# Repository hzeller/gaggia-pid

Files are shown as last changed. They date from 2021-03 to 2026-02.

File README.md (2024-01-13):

PID controller for Gaggia Classic
=================================

# Temperature Sensor
Using the [Max31725] for nice high accuracy and fast temperature updates. Also
a bit overengineered, but that is what I had lying around.

The sensor is on a little PCB (which you find in the
[sensor-mount/](./sensor-mount) directory. Glued into the existing brass
screw-cups the original bimetallic sensor was in (using JB Weld, which is
a sufficiently high-temperature epoxy), then wired up with silicone wiring and
sealed with silicone.

Mount on the side of the boiler where the original brew temp sensor was.

PCB            | Preparing mount | Glued in cup | Sealed
---------------|-----------------|--------------|--------
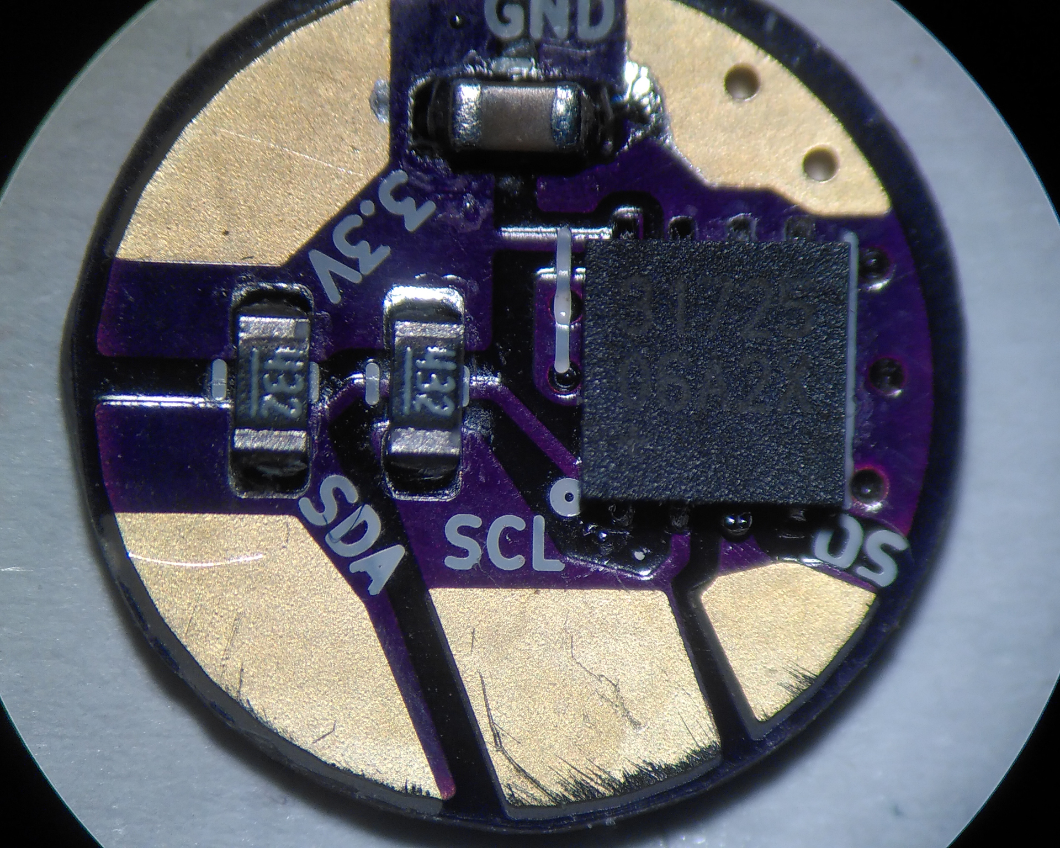
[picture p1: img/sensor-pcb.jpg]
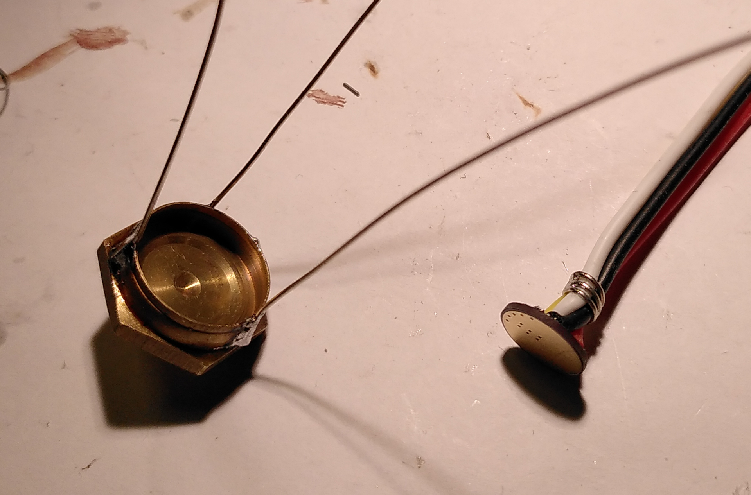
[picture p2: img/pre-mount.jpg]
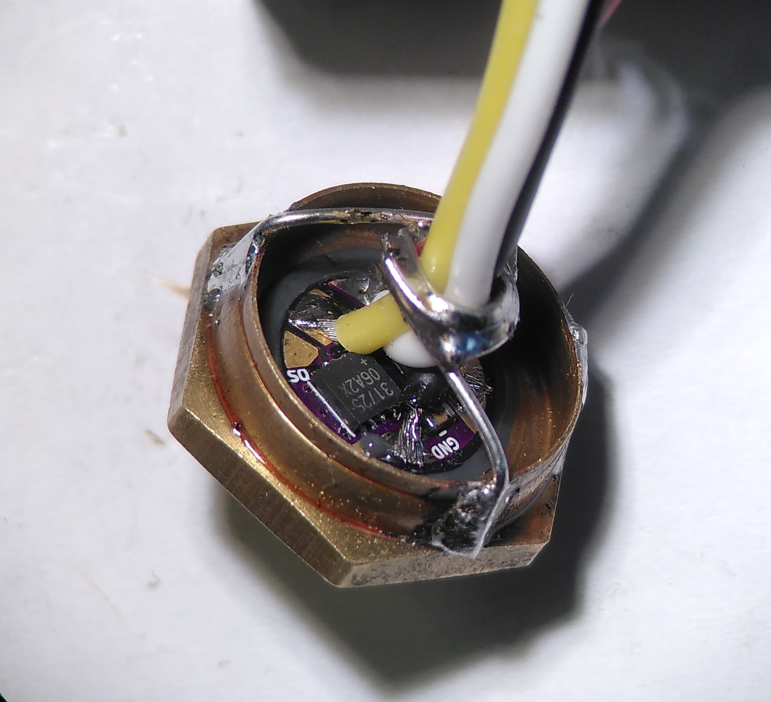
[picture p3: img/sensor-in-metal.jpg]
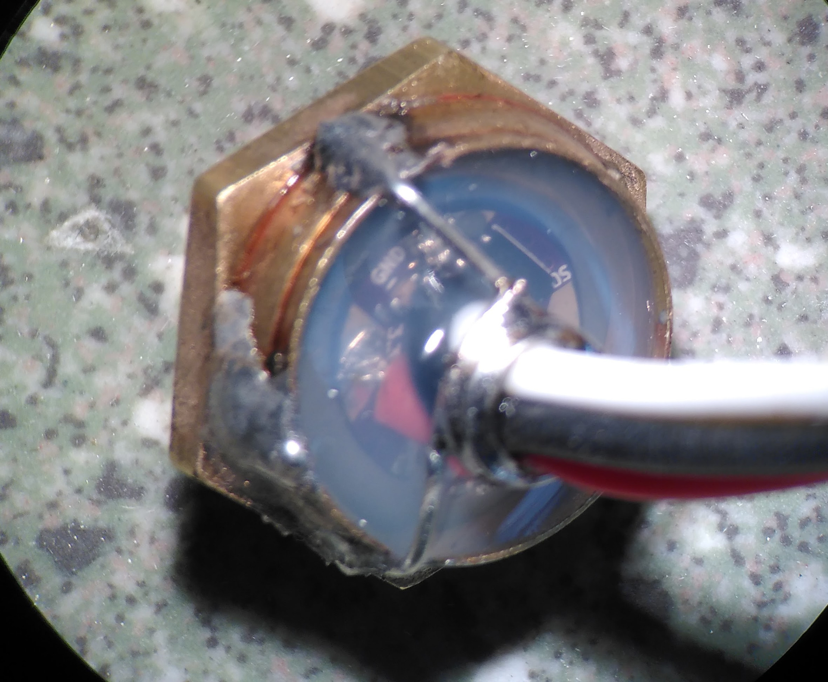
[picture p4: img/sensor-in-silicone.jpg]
 |  |  | 

# PID Controller

Runs on a conventional Arduino Nano.

To program, get avr-gcc and avrdude. The Makefile takes care of compiling
and flashing:

```
cd firmware
make flash
```

The sytem is powered with a sealed 5V power supply CUI PSK-3D-5.
The Solid State Relay is a Panasonic AQJ112V.

The USB connector is arranged in a way that it is reachable through one of the
opening on the back. From the front, the machine is entirely unaltered (unlike
many of the somewhat ugly PID mods of this machine).

You connect with a serial console to the PID controller, adjust
PID parameters and watch an ASCII-art 'graphical' output of the temperature
sensor (see the picture with the Laptop in view and the rising temperature
displayed).

PID parameters can be tuned with the interface presented on the serial
interface and stored in EEPROM.

Serial interface running by default on 38400 bps:

```bash
tio -b 38400 /dev/ttyUSB0
```

Menu:
```
#            ☕ Gaggia PID controller
#(c) 2021 Henner Zeller  |  GNU Public License
#Commands
#       l - Start log to console. Stop with any key.
#       L - Ditto. With 'graph'
#       n - Now. Print PID parameters, last temp and control out.
#
#       s <setpoint> - set setpoint.
#       p <Kp>       - set proportional gain.
#       i <Ki>       - set integral gain.
#       d <Kd>       - set derivative gain.
#
#       w - Write PID parameters to EEPROM.
#       r - Restore PID parameters from EEPROM.
#       h - This help
```

Components         | Mounted | Back  | Settings via USB
-------------------|---------|-------|--------------------------
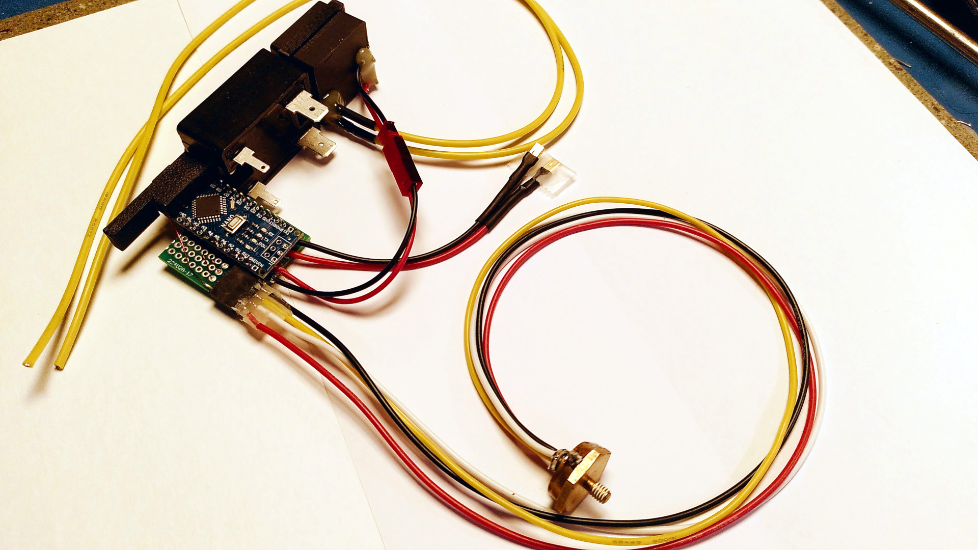
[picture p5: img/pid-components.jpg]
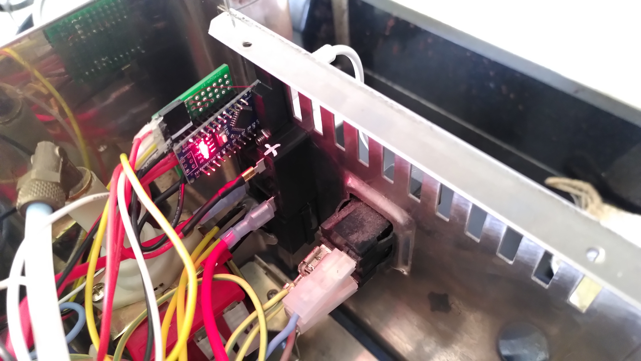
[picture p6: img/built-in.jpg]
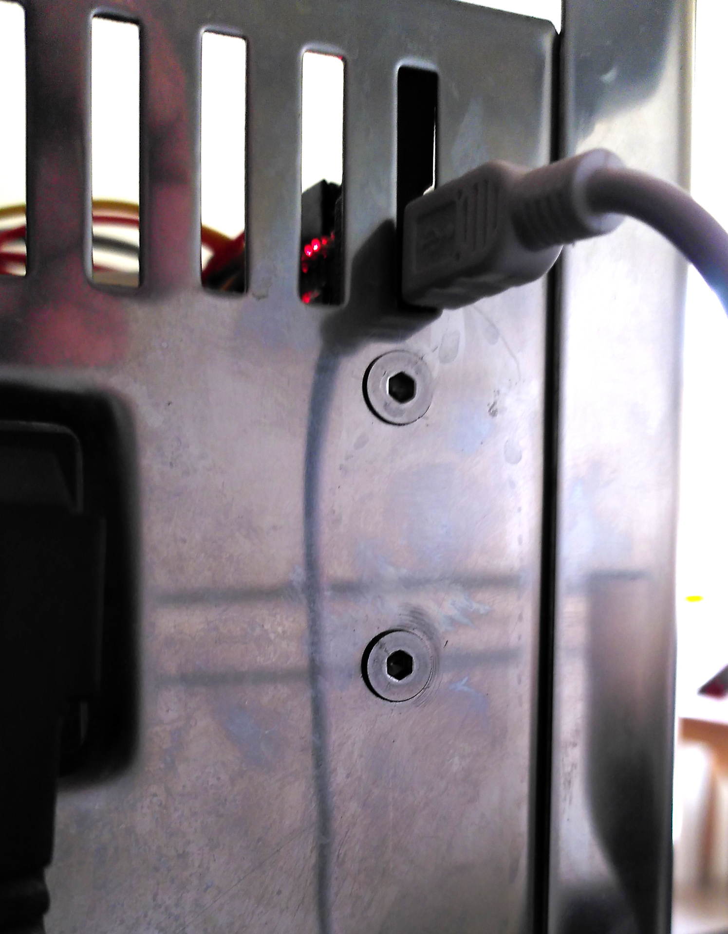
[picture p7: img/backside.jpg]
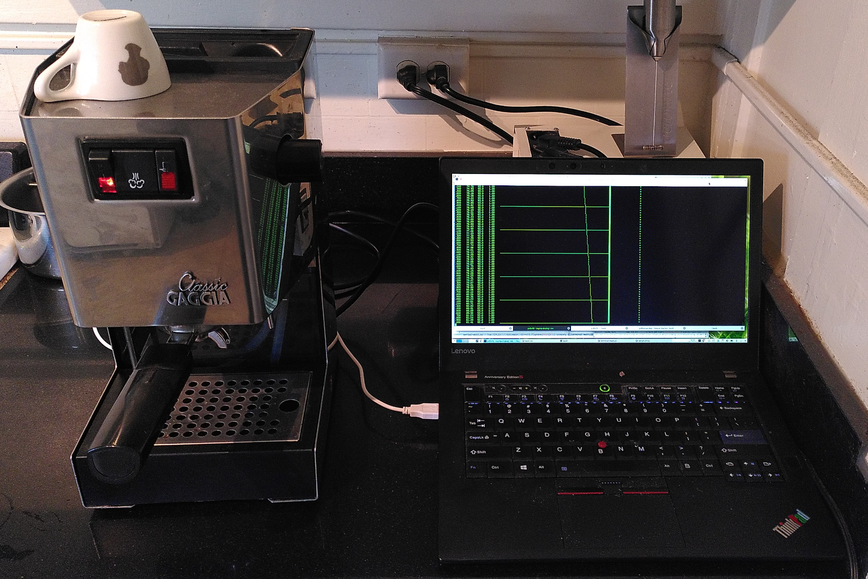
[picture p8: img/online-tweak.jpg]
 |  |  | 

[Max31725]: https://datasheets.maximintegrated.com/en/ds/MAX31725-MAX31726.pdf

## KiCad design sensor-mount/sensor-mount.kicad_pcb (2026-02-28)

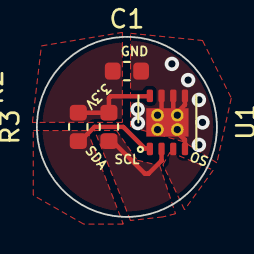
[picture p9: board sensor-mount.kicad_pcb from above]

Board: 2 copper layers, 10.0 x 10.0 mm, 4 parts (0 on the bottom side), 4 nets.

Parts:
C1: 220n; C_0603_1608Metric
R2, R3: 4k7; R_0603_1608Metric
U1: MAX31725; DFN-8-1EP_3x3mm_P0.65mm_EP1.7x2.05mm

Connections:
/SCL: R2.2, U1.2 (SCL)
/SDA: R3.2, U1.1 (SDA)
GND: C1.2, U1.4 (GND), U1.5 (A2), U1.6 (A1), U1.7 (A0), U1.9 (EP)
VCC: C1.1, R2.1, R3.1, U1.8 (VDD)

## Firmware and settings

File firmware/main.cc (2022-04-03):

// -*- mode: c++; c-basic-offset: 2; indent-tabs-mode: nil; -*-
//
// Copyright (C) 2021 Henner Zeller <h.zeller@acm.org>
//
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
#include <math.h>
#include <stdlib.h>
#include <string.h>

#include <avr/eeprom.h>
#include <avr/interrupt.h>
#include <avr/io.h>
#include <avr/sleep.h>

#include "i2c-master.h"
#include "max31725.h"
#include "pid.h"
#include "progmem.h"
#include "serial-com.h"
#include "serial-util.h"
#include "strfmt.h"

/* Note, we have plenty of flash, so we use the luxory of float numbers */

/*
 * Regular interval to take measurements and calculate a new PID control output
 */
static constexpr uint16_t kTimeBaseMs = 50;

static struct ConfigData {
  char dummy;  // Leave first char free, sometimes containing garbage.

  // PID info.
  float setpoint;
  float kp;
  float ki;
  float kd;

  void Write() {
    eeprom_write_float(&setpoint, setpoint);
    eeprom_write_float(&kp, kp);
    eeprom_write_float(&ki, ki);
    eeprom_write_float(&kd, kd);
  }
  void Read() {
    setpoint = eeprom_read_float(&setpoint);
    kp = eeprom_read_float(&kp);
    ki = eeprom_read_float(&ki);
    kd = eeprom_read_float(&kd);
  }
} EEMEM eeConfigData;

// Read number from serial and indicate if it was successful.
// Pre-fill the editline with the existing number with given digits.
static bool readNumber(SerialCom *comm, float *value, int digits) {
  char buffer[10];
  strcpy(buffer, strfmt_float(*value, digits));
  const char *str = readln(comm, buffer, sizeof(buffer), true);
  char *endptr = nullptr;
  float converted = strtod(str, &endptr);
  if (endptr != str) {
    *value = converted;
    println(comm, _P(" ✓"));
    return true;
  } else {
    println(comm, _P(" ✗ (not changed)"));
    return false;
  }
}

// A slow PWM of the heater. There is not much point in high-speed PWM with
// a zero-cross SSD, so we manually trigger with a timer interrupt.
// We go through one full cycle in kRange time interrupts.
//
// For safety, the value needs to be set for each cycle individually, otherwise
// we fail-safe to zero output.
class HeaterPWM {
  static constexpr uint8_t PORTB_LED_BIT = (1<<5);
  static constexpr uint8_t PORTD_SSR_BIT = (1<<3);

public:
  static constexpr uint8_t kRange = 32;

  HeaterPWM() {
    DDRB |= PORTB_LED_BIT;
    DDRD |= PORTD_SSR_BIT;
    SetOn(false);  // Safe starting point.
  }

  // Value of 0..1.0
  // For safety, needs to be actively set once per period, otherwise will
  // fall-back to zero. This prevents lock-up situations.
  void SetValue(float v) {
    if (v < 0.0) v = 0;
    if (v > 1.0) v = 1.0;
    value_ = v * kRange;
  }

  void HandleTimeInterrupt(uint8_t global_time) volatile {
    if ((global_time % kRange) == 0) {
      pwm_state_ = value_;
      value_ = 0;  // Will require to SetValue() again.
    }

    SetOn(pwm_state_ != 0);
    if (pwm_state_ > 0) --pwm_state_;
  }

private:
  void SetOn(bool b) volatile {
    if (b) {
      PORTB |= PORTB_LED_BIT;
      PORTD |= PORTD_SSR_BIT;
    } else {
      PORTB &= ~PORTB_LED_BIT;
      PORTD &= ~PORTD_SSR_BIT;
    }
  }

  volatile uint8_t value_ = 0;      // Range from 0x00..kRange
  volatile uint8_t pwm_state_ = 0;  // Current PWM counter.
};

// There is only one global instance, accessible to the timer interrupt
static HeaterPWM sHeater;

/*
 * Setting up timer to trigger an interrupt every kTimeBaseMs
 */
static constexpr uint16_t kTimerCounts = F_CPU / 256 * kTimeBaseMs / 1000;
static constexpr uint16_t kTimerRegister = 65535 - kTimerCounts;

// Global time, increasing with timer interrupt. Wrapping around at 8 bit.
volatile uint8_t sGlobalTime = 0;

ISR(TIMER1_OVF_vect) {
  sGlobalTime++;
  TCNT1 = kTimerRegister;
  sHeater.HandleTimeInterrupt(sGlobalTime);
}

void initTimer() {
  TCNT1 = kTimerRegister;
  TCCR1A = 0x00;
  TCCR1B = (1 << CS12); // prescale 256 (also see kTimerCounts)
  TIMSK1 = (1 << TOIE1);
}

// Print temperature and control value, and show in 'graphical' form.
void printTemp(SerialCom *com, bool markline,
               float measured, float control_value,
               float target_temp,
               bool with_graph) {
  const ProgmemPtr vt100Underline = _P("\e[4m");
  const ProgmemPtr vt100Inverse   = _P("\e[7m");
  const ProgmemPtr vt100Reset     = _P("\e[0m");

  // Raw values, formatted with tab to be easily parsed if needed.
  printRAM(com, strfmt_float(measured, 2));
  com->write('\t');
  printRAM(com, strfmt_float(target_temp, 1));
  com->write('\t');
  printRAM(com, strfmt_float(control_value, 2));
  com->write('\t');

  if (!with_graph) {
    println(com);
    return;
  }

  control_value *= 100.0f;  // Display in percent.

  // Useful for human consumption: some graph representation of above values
  constexpr float kBaselineOffset = 15;  // Cut off boring lower part.
  const uint8_t degree_display = measured - kBaselineOffset;
  const uint8_t target_display = target_temp > kBaselineOffset ?
    target_temp - kBaselineOffset : 0;
  uint8_t max_run = target_display;
  if (degree_display > max_run) max_run = degree_display;
  if (control_value > max_run)  max_run = control_value;

  const int decidegrees = 10.0f * measured;
  bool reset_needed = markline || target_display > 0;
  if (markline) print(com, vt100Underline);
  for (uint8_t s = 0; s < max_run+1; ++s) {
    // The target temperature is an inverted character cell, so that we can
    // see the temperature line 'underneath'.
    if (s > 0 && s == target_display) print(com, vt100Inverse);

    if (s == degree_display) {     // These are full degrees
      switch (decidegrees % 10) {  // Graphically divide decis into sub-blocks
      case 0: case 1: case 2:         print(com, _P("\u258f")); break;
      case 3: case 4: case 5: case 6: print(com, _P("|"));      break;
      case 7: case 8: case 9:         print(com, _P("\u2595")); break;
      }
    }
    else if (s == (uint8_t)control_value)
      com->write('*');
    else
      com->write(' ');

    if (s > 0 && s == target_display) {
      print(com, vt100Reset);
      reset_needed = false;
    }
  }

  if (reset_needed) print(com, vt100Reset);
  println(com);
}

void printUsage(SerialCom *com) {
  // Prefix all lines with '#' to make it easy to filter out lines meant
  // for human consumption.
  print(com,
        _P("#\e[7m            ☕ Gaggia PID controller            \e[0m\r\n"
           "#(c) 2021 Henner Zeller  |  GNU Public License\r\n"
           "#Commands\r\n"
           "#\tl - Start log to console. Stop with any key.\r\n"
           "#\tL - Ditto. With 'graph'\r\n"
           "#\tn - Now. Print PID parameters, last temp and control out.\r\n"
           "#\r\n"
           "#\ts <setpoint> - set setpoint.\r\n"
           "#\tp <Kp>       - set proportional gain.\r\n"
           "#\ti <Ki>       - set integral gain.\r\n"
           "#\td <Kd>       - set derivative gain.\r\n"
           "#\r\n"
           "#\tw - Write PID parameters to EEPROM.\r\n"
           "#\tr - Restore PID parameters from EEPROM.\r\n"
           "#\th - This help\r\n"
           ));
}

int main() {
  I2CMaster::Init();
  initTimer();

  // PID interval once per full PWM cycle.
  PID pid(HeaterPWM::kRange * kTimeBaseMs * 0.001);
  Max31725TempSensor sensor;
  SerialCom com;

  uint8_t last_measure_period = 0;

  float measured_temp = 42.0;
  float pid_control_output = 0.0f;

  // Logging enable status and its current time.
  bool logging = false;
  bool logging_with_graph = false;
  uint16_t log_time = 0;

  // Serial line connect apparently resets Arduino Nano.
  // Use that as an opportunity to print welcome and usage message.
  printUsage(&com);

  eeConfigData.Read();
  pid.FromConfig(eeConfigData);

  // Get ready to sleep. We're only doing anything when timer or serial calls.
  sleep_enable();
  sei();

  const ProgmemPtr kLoggingCSVHeader = _P("TIME\tTEMP\tTARGET\tCONTROL");
  for (;;) {
    sleep_cpu();  // Wake on interrupts from timer or serial.

    if (sGlobalTime != last_measure_period) {  // timer triggered
      last_measure_period = sGlobalTime;
      measured_temp = sensor.GetTemp();

      // Update the PID just before the heater starts its next PWM cycle.
      if (last_measure_period % HeaterPWM::kRange == HeaterPWM::kRange - 1) {
        pid_control_output = pid.Update(measured_temp);
        sHeater.SetValue(pid_control_output);
      }

      if (logging) {
        printRAM(&com, strfmt(log_time, 3));
        com.write('\t');
        printTemp(&com, log_time==0, measured_temp, pid_control_output,
                  pid.setpoint, logging_with_graph);
        log_time += kTimeBaseMs;
        log_time %= 1000;
      }
    }

    // Check for commands.
    while (com.read_available()) {
      const char c = com.read();
      if (logging) {   // stops at any key. Consume it.
        logging = false;
        println(&com, _P("# logging stopped."));
        continue;
      }
      switch (c) {
      case 'l':    // Trigger logging.
      case 'L':    // ... with graph.
        logging = true;
        logging_with_graph = (c == 'L');
        println(&com, _P("# logging started. Stop with any key."));
        println(&com, kLoggingCSVHeader);
        break;

      case 's':
        print(&com, _P("set setpoint = "));
        readNumber(&com, &pid.setpoint, 1);
        pid.Sanitize();
        pid.Print(&com, false);
        break;

      case 'p':
        print(&com, _P("set Kp = "));
        readNumber(&com, &pid.kp, 3);
        pid.Sanitize();
        pid.Print(&com, false);
        break;

      case 'i':
        print(&com, _P("set Ki = "));
        readNumber(&com, &pid.ki, 3);
        pid.Sanitize();
        pid.Print(&com, false);
        break;

      case 'd':
        print(&com, _P("set Kd = "));
        readNumber(&com, &pid.kd, 3);
        pid.Sanitize();
        pid.Print(&com, false);
        break;

      case 'n':
        pid.Print(&com, true);
        break;

      case 'w':
        println(&com, _P("Storing PID parameters to EEPROM."));
        pid.Print(&com, false);
        pid.ToConfig(&eeConfigData);
        eeConfigData.Write();
        break;

      case 'r':
        println(&com, _P("Restore PID parameters from EEPROM."));
        eeConfigData.Read();
        pid.FromConfig(eeConfigData);
        pid.Print(&com, false);
        break;

      case '\r': case '\n':
        // Ignore. Allows to idempotently reset logging before starting with 'l'
        break;

      default:
        com.write(c);
        println(&com, _P(" : Unknown command."));
        /* fallthrough */
      case '?': case 'h':
        printUsage(&com);
        break;
      }
    }
  }
}

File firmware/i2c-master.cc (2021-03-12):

// -*- mode: c++; c-basic-offset: 2; indent-tabs-mode: nil; -*-
//
// Copyright (C) 2018 Henner Zeller <h.zeller@acm.org>
//
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
#include "i2c-master.h"

#include <util/twi.h>
#include <avr/io.h>

// These are for ATMega328p
#define I2C_DDR       DDRC
#define I2C_PORT      PORTC
#define I2C_PORT_SDA  4
#define I2C_PORT_SCL  5

static constexpr uint32_t TX_SPEED = 400000;
static constexpr uint8_t PRESCALER = 1;
static constexpr uint8_t TWBR_val = (((F_CPU/TX_SPEED) / PRESCALER) - 16 ) / 2;

void I2CMaster::Init() {
  TWBR = TWBR_val;
}

void I2CMaster::Enable(bool en) {
  if (en) {
    I2C_PORT |= (1<<I2C_PORT_SDA) | (1<<I2C_PORT_SCL);     // pullups on.
    I2C_DDR |= (1<<I2C_PORT_SDA) | (1<<I2C_PORT_SCL);      // set output
  } else {
    I2C_PORT &= ~((1<<I2C_PORT_SDA) | (1<<I2C_PORT_SCL));  // pullups off.
    I2C_DDR &= ~((1<<I2C_PORT_SDA) | (1<<I2C_PORT_SCL));
  }
}

void I2CMaster::StartTransmission(uint8_t address) {
  TWCR = 0;
  TWCR = (1<<TWINT) | (1<<TWSTA) | (1<<TWEN);  // start condition
  while (!(TWCR & (1<<TWINT)))  // Wait to finish transmit
    ;

  if ((TWSR & 0xF8) != TW_START)   // Something went wrong.
    return;

  Write(address);
}

void I2CMaster::Write(uint8_t b) {
  TWDR = b;
  TWCR = (1<<TWINT) | (1<<TWEN);  // start transmission.
  while (!(TWCR & (1<<TWINT)))    // wait finish.
    ;
}

uint8_t I2CMaster::Read(bool ack) {
  TWCR = (1<<TWINT) | (1 << TWEN) | (ack << TWEA);
  while (!(TWCR & (1<<TWINT)))    // wait finish.
    ;
  return TWDR;
}

void I2CMaster::FinishTransmission() {
  TWCR = (1<<TWINT) | (1<<TWEN) | (1<<TWSTO);
}

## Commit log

2021-03-07 Initial version.
    [sensor-mount.kicad_pcb, sensor-mount.kicad_sch]
2021-03-07 The Maxim footprint has 0.65mm pitch.
    [sensor-mount.kicad_pcb, sensor-mount.kicad_sch]
2021-03-12 Start firmware. For now, just read temperature from MAX31725 and display.
    * Regularly read temperature sensor (using a timer interrupt).
    * Provide a simple serial interface to query temperature and
    output a log with an character 'graph'.
    * Show current temperature on a SH1106 display.
    * No PID calculation or output yet.
    Temperature sensor and SH1106 are connected to the same i2c bus.
2022-03-07 Add low-speed PWM to switch heater.
2022-03-09 Switch to float to represent real values.
    Easier to handle than fixed point. Since we have enough program
    flash capacity and do very little calculations, this is doable.
    [main.cc, max31725.cc]
2022-03-11 Editing: beep when line too long.
    [main.cc]
2022-03-11 Prevent setting invalid values.
    [main.cc]
2022-03-12 Move PID and serial utility functions into their own files.
2022-03-14 Improve anti-windup.
    Stop integrating if we are already clamping the output and integration
    would contribute to more output overshoot that we have to decay later.
2022-03-14 Higher resolution for the heater PWM (32 vs. 16 levels).
2022-08-14 Upgrade to latest kicad; fix missing symbol library config.
    [sensor-mount.kicad_pcb, sensor-mount.kicad_sch]
2022-08-14 Fix path to 3D models.
    [sensor-mount.kicad_pcb]
2026-02-28 Update kicad outputs to latest
    [sensor-mount.kicad_pcb, sensor-mount.kicad_sch]
2026-02-28 Exclude local kicad stuff in gitignore

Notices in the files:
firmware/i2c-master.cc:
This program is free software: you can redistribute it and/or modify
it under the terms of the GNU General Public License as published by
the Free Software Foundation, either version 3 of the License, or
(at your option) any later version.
